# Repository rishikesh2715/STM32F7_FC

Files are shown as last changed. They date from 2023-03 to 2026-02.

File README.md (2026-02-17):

# I am going to be working on a new design of this flight controller.

- Removing AT7456E based analog OSD and CVBS routing.
- Targeting modern digital FPV systems.
- Feel free to recommend any changes you wanna see. Just open an issue.

Hoping to have the new hardware done next month if life chills out. 

# STM32F7_Based_FLight-controller
STM32F722RET6 Based Flight Controller with ICM-42688-P IMU, BMP388 Barometer, and much more!

Detailed Specification:
- MCU - STM32F722RET6
- Interial Measurement Unit (IMU) - ICM-42688-P
- Barometer - BMP388
- On-screen Display chip (OSD) - AT7456E
- SPI FLASH - W25Q256JVEIQ (256 Mbit QUAD SPI NOR FLASH)
- 9 V -- 2A Buck Converter - TPS54335ADRCR
- 5V -- 2A Buck Converter - TPS54335ADRCR
- 3.3 V -- 700 mA LDO - AZ1117-3.3

Connectors:
- 4 UARTs
- 3 SPIs
- 1 I2C

This flight controller is directly flashable and configurale via BetaFlight. Make sure to flash the FC with custom CLI file named "IRS_CLI". There is a official tutorial on youtube on how to flash a custom flight controller with a custom cli file.

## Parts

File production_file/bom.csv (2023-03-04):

Designator | Footprint | Quantity | Value | LCSC Part #
TP19 | Solderable Point | 1 | G
TP6 | Solderable Point | 1 | G
TP5 | Solderable Point | 1 | G
D3 | LED_0402_1005Metric | 1 | LED
C39 | C_0201_0603Metric | 1 | 100n
TP4 | Solderable Point | 1 | DJI_RX
TP8 | Solderable Point | 1 | G
TP12 | Solderable Point | 1 | 3.3V
TP11 | Solderable Point | 1 | 3.3V
TP10 | Solderable Point | 1 | G
C46 | C_0201_0603Metric | 1 | 100n
FB1 | R_0603_1608Metric | 1 | 120R
R14 | R_0402_1005Metric | 1 | 550R
H3 | MountingHole_2.2mm_M2_Pad_Via | 1 | MountingHole
R6 | R_0201_0603Metric | 1 | 4K7
U8 | LQFP-64_10x10mm_P0.5mm | 1 | STM32F722RET6
TP20 | Solderable Point | 1 | G
C44 | C_0402_1005Metric | 1 | 1u
TP21 | Solderable Point | 1 | G
C41 | C_0201_0603Metric | 1 | 100n
C17 | C_0805_2012Metric | 1 | 10u
R18 | R_0402_1005Metric | 1 | 10K
H4 | MountingHole_2.2mm_M2_Pad_Via | 1 | MountingHole
C38 | C_0402_1005Metric | 1 | 1u
R29 | R_0402_1005Metric | 1 | 550R
L1 | MDE0530-6R8M | 1 | 3u2, IDC 5.4A
C16 | C_0805_2012Metric | 1 | 10u
C28 | C_0603_1608Metric | 1 | 1n8
C19 | C_0805_2012Metric | 1 | 10u
H1 | MountingHole_2.2mm_M2_Pad_Via | 1 | MountingHole
C32 | C_1210_3225Metric | 1 | 47u
R27 | R_0603_1608Metric | 1 | 330R
C45 | C_0201_0603Metric | 1 | 100n
TP18 | Solderable Point | 1 | G
TP13 | Solderable Point | 1 | 5V
R16 | R_0402_1005Metric | 1 | 31K
R15 | R_0402_1005Metric | 1 | 31K
C34 | C_0402_1005Metric | 1 | 10p
D4 | LED_0402_1005Metric | 1 | LED
R11 | R_0201_0603Metric | 1 | 27R
C12 | C_0201_0603Metric | 1 | 100n
R7 | R_0201_0603Metric | 1 | 4K7
C35 | C_0402_1005Metric | 1 | 10p
TP16 | Solderable Point | 1 | 9V
C13 | C_0201_0603Metric | 1 | 100n
C42 | C_0201_0603Metric | 1 | 100n
J10 | JST_SH_SM04B-SRSS-TB_1x04-1MP_P1.00mm_Horizontal | 1 | Conn_01x04
TP2 | Solderable Point | 1 | DJI_TX
R12 | R_0201_0603Metric | 1 | 27R
J9 | Tag-Connect_TC2030-IDC-NL_2x03_P1.27mm_Vertical | 1 | TC2030-IDC-NL
TP3 | Solderable Point | 1 | GRX
C30 | C_1210_3225Metric | 1 | 47u
D5 | LED_0402_1005Metric | 1 | LED
L2 | MDE0530-6R8M | 1 | 2u7, IDC 4A
H2 | MountingHole_2.2mm_M2_Pad_Via | 1 | MountingHole
C23 | C_0402_1005Metric | 1 | 100n
TP1 | Solderable Point | 1 | GTX
C24 | C_0402_1005Metric | 1 | 100n
R13 | R_0402_1005Metric | 1 | 550R
C47 | C_0603_1608Metric | 1 | 2u2
C36 | C_0603_1608Metric | 1 | 4u7
C33 | C_1210_3225Metric | 1 | 47u
C40 | C_0201_0603Metric | 1 | 100n
U7 | TPS54335ADRCR | 1 | TPS54335ADRCR
C37 | C_0402_1005Metric | 1 | 10u
R23 | R_0402_1005Metric | 1 | 0R
Y2 | Crystal_SMD_3225-4Pin_3.2x2.5mm | 1 | 8Mhz
U6 | TPS54335ADRCR | 1 | TPS54335ADRCR
TP15 | Solderable Point | 1 | 9V
C21 | C_0402_1005Metric | 1 | 100n
C20 | C_0402_1005Metric | 1 | 100n
C26 | C_0201_0603Metric | 1 | 91p
C18 | C_0805_2012Metric | 1 | 10u
U3 | BMP388 | 1 | BMP388
J12 | JST_SH_SM06B-SRSS-TB_1x06-1MP_P1.00mm_Horizontal | 1 | Conn_01x06
C10 | C_0201_0603Metric | 1 | 10n
C22 | C_0805_2012Metric | 1 | 22u
C1 | C_0201_0603Metric | 1 | 10p
J5 | JST_SH_SM08B-SRSS-TB_1x08-1MP_P1.00mm_Horizontal | 1 | FC-ESC
C2 | C_0201_0603Metric | 1 | 10p
R20 | R_0402_1005Metric | 1 | 9K7
R1 | R_0201_0603Metric | 1 | 75R
R5 | R_0201_0603Metric | 1 | 0R
C27 | C_0603_1608Metric | 1 | 1n8
C8 | C_0201_0603Metric | 1 | 22u
J8 | JST_SH_SM06B-SRSS-TB_1x06-1MP_P1.00mm_Horizontal | 1 | Conn_01x06
Y1 | Crystal_SMD_3225-4Pin_3.2x2.5mm | 1 | 27MHz
R25 | R_0201_0603Metric | 1 | 1K
C15 | C_0805_2012Metric | 1 | 10u
Q1 | SOT-23 | 1 | DMG3415
C3 | C_0201_0603Metric | 1 | 100n
R19 | R_0402_1005Metric | 1 | 100K
U4 | SON127P600X800X80-9N | 1 | W25Q256JVEIQ
J2 | JST_SH_SM03B-SRSS-TB_1x03-1MP_P1.00mm_Horizontal | 1 | Conn_01x03
C43 | C_0402_1005Metric | 1 | 0.1u
R3 | R_0201_0603Metric | 1 | 75R
C6 | C_0201_0603Metric | 1 | 100n
R2 | R_0201_0603Metric | 1 | 10K
C5 | C_0201_0603Metric | 1 | 22u
C25 | C_0201_0603Metric | 1 | 91p
R10 | R_0201_0603Metric | 1 | 5K1
SW1 | SSSS810701 | 1 | SW_SPDT
J1 | JST_SH_SM03B-SRSS-TB_1x03-1MP_P1.00mm_Horizontal | 1 | Conn_01x03
C4 | C_0402_1005Metric | 1 | 0.1u
U5 | SOT-223-3_TabPin2 | 1 | AZ1117-ADJ
J6 | JST_SH_SM04B-SRSS-TB_1x04-1MP_P1.00mm_Horizontal | 1 | Conn_01x04
C9 | C_0201_0603Metric | 1 | 100n
J3 | JST_SH_SM03B-SRSS-TB_1x03-1MP_P1.00mm_Horizontal | 1 | Conn_01x03
R22 | R_0201_0603Metric | 1 | 19K1
D1 | D_SOD-123 | 1 | RB088LAM-40TFR
R9 | R_0201_0603Metric | 1 | 5K1
R26 | R_0402_1005Metric | 1 | 10K
C7 | C_0603_1608Metric | 1 | 2u2
R17 | R_0402_1005Metric | 1 | 10K
C29 | C_1210_3225Metric | 1 | 47u
C14 | C_0402_1005Metric | 1 | 100n
C11 | C_0201_0603Metric | 1 | 100n
R24 | R_0201_0603Metric | 1 | 10K
C31 | C_1210_3225Metric | 1 | 47u
J4 | JST_SH_SM03B-SRSS-TB_1x03-1MP_P1.00mm_Horizontal | 1 | Conn_01x03
J11 | JST_SH_SM04B-SRSS-TB_1x04-1MP_P1.00mm_Horizontal | 1 | Conn_01x04
R8 | R_0201_0603Metric | 1 | 10K
D2 | SOT-143 | 1 | PRTR5V0U2X
JP1 | SolderJumper-2_P1.3mm_Open_TrianglePad1.0x1.5mm | 1 | NRST
U2 | SOP65P637X110-28N | 1 | AT7456E
R21 | R_0201_0603Metric | 1 | 100K
J7 | JST_SH_SM06B-SRSS-TB_1x06-1MP_P1.00mm_Horizontal | 1 | DJI Air Unit
P1 | USB4110GFA | 1 | USB_C_Plug_USB2.0
R4 | R_0201_0603Metric | 1 | 0R
R28 | R_0201_0603Metric | 1 | 100K
U1 | ICP-42688-P | 1 | ICM-42688-P

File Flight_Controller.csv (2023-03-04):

Source: | C:\Users\RISHIKESH\OneDrive\Documents\Flight Controller\Flight_Controller\Flight_Controller.kicad_sch
Date: | 1/20/2023 8:09:45 PM
Tool: | Eeschema (6.0.4)
Generator: | E:\New folder (2)\Streamlabs OBS\KiCad\6.0\bin\scripting\plugins/bom_csv_grouped_by_value.py
Component Count: | 131
Individual Components:
Item | Qty | Reference(s) | Value | LibPart | Footprint | Datasheet | MANUFACTURER | MAXIMUM_PACKAGE_HEIGHT | Manufacturer | PARTREV | Package | STANDARD
 |  | C1 | 10p | Device:C_Small | Capacitor_SMD:C_0201_0603Metric | ~
 |  | C2 | 10p | Device:C_Small | Capacitor_SMD:C_0201_0603Metric | ~
 |  | C3 | 100n | Device:C_Small | Capacitor_SMD:C_0201_0603Metric | ~
 |  | C4 | 0.1u | Device:C_Small | Capacitor_SMD:C_0402_1005Metric | ~
 |  | C5 | 22u | Device:C_Small | Capacitor_SMD:C_0201_0603Metric | ~
 |  | C6 | 100n | Device:C_Small | Capacitor_SMD:C_0201_0603Metric | ~
 |  | C7 | 2u2 | Device:C_Small | Capacitor_SMD:C_0603_1608Metric | ~
 |  | C8 | 22u | Device:C_Small | Capacitor_SMD:C_0201_0603Metric | ~
 |  | C9 | 100n | Device:C_Small | Capacitor_SMD:C_0201_0603Metric | ~
 |  | C10 | 10n | Device:C_Small | Capacitor_SMD:C_0201_0603Metric | ~
 |  | C11 | 100n | Device:C_Small | Capacitor_SMD:C_0201_0603Metric | ~
 |  | C12 | 100n | Device:C_Small | Capacitor_SMD:C_0201_0603Metric | ~
 |  | C13 | 100n | Device:C_Small | Capacitor_SMD:C_0201_0603Metric | ~
 |  | C14 | 100n | Device:C_Small | Capacitor_SMD:C_0402_1005Metric | ~
 |  | C15 | 10u | Device:C_Small | Capacitor_SMD:C_0805_2012Metric | ~
 |  | C16 | 10u | Device:C_Small | Capacitor_SMD:C_0805_2012Metric | ~
 |  | C17 | 10u | Device:C_Small | Capacitor_SMD:C_0805_2012Metric | ~
 |  | C18 | 10u | Device:C_Small | Capacitor_SMD:C_0805_2012Metric | ~
 |  | C19 | 10u | Device:C_Small | Capacitor_SMD:C_0805_2012Metric | ~
 |  | C20 | 100n | Device:C_Small | Capacitor_SMD:C_0402_1005Metric | ~
 |  | C21 | 100n | Device:C_Small | Capacitor_SMD:C_0402_1005Metric | ~
 |  | C22 | 22u | Device:C_Small | Capacitor_SMD:C_0805_2012Metric | ~
 |  | C23 | 100n | Device:C_Small | Capacitor_SMD:C_0402_1005Metric | ~
 |  | C24 | 100n | Device:C_Small | Capacitor_SMD:C_0402_1005Metric | ~
 |  | C25 | 91p | Device:C_Small | Capacitor_SMD:C_0201_0603Metric | ~
 |  | C26 | 91p | Device:C_Small | Capacitor_SMD:C_0201_0603Metric | ~
 |  | C27 | 1n8 | Device:C_Small | Capacitor_SMD:C_0603_1608Metric | ~
 |  | C28 | 1n8 | Device:C_Small | Capacitor_SMD:C_0603_1608Metric | ~
 |  | C29 | 47u | Device:C_Small | Capacitor_SMD:C_1210_3225Metric | ~
 |  | C30 | 47u | Device:C_Small | Capacitor_SMD:C_1210_3225Metric | ~
 |  | C31 | 47u | Device:C_Small | Capacitor_SMD:C_1210_3225Metric | ~
 |  | C32 | 47u | Device:C_Small | Capacitor_SMD:C_1210_3225Metric | ~
 |  | C33 | 47u | Device:C_Small | Capacitor_SMD:C_1210_3225Metric | ~
 |  | C34 | 10p | Device:C_Small | Capacitor_SMD:C_0402_1005Metric | ~
 |  | C35 | 10p | Device:C_Small | Capacitor_SMD:C_0402_1005Metric | ~
 |  | C36 | 4u7 | Device:C_Small | Capacitor_SMD:C_0603_1608Metric | ~
 |  | C37 | 10u | Device:C | Capacitor_SMD:C_0402_1005Metric | ~
 |  | C38 | 1u | Device:C | Capacitor_SMD:C_0402_1005Metric | ~
 |  | C39 | 100n | Device:C | Capacitor_SMD:C_0201_0603Metric | ~
 |  | C40 | 100n | Device:C | Capacitor_SMD:C_0201_0603Metric | ~
 |  | C41 | 100n | Device:C | Capacitor_SMD:C_0201_0603Metric | ~
 |  | C42 | 100n | Device:C | Capacitor_SMD:C_0201_0603Metric | ~
 |  | C43 | 0.1u | Device:C_Small | Capacitor_SMD:C_0402_1005Metric | ~
 |  | C44 | 1u | Device:C | Capacitor_SMD:C_0402_1005Metric | ~
 |  | C45 | 100n | Device:C | Capacitor_SMD:C_0201_0603Metric | ~
 |  | C46 | 100n | Device:C | Capacitor_SMD:C_0201_0603Metric | ~
 |  | C47 | 2u2 | Device:C_Small | Capacitor_SMD:C_0603_1608Metric | ~
 |  | D1 | RB088LAM-40TFR | Device:D_Schottky | Diode_SMD:D_SOD-123 | ~
 |  | D2 | PRTR5V0U2X | Power_Protection:PRTR5V0U2X | Package_TO_SOT_SMD:SOT-143 | https://assets.nexperia.com/documents/data-sheet/PRTR5V0U2X.pdf
 |  | D3 | LED | Device:LED | LED_SMD:LED_0402_1005Metric | ~
 |  | D4 | LED | Device:LED | LED_SMD:LED_0402_1005Metric | ~
 |  | D5 | LED | Device:LED | LED_SMD:LED_0402_1005Metric | ~
 |  | FB1 | 120R | Device:FerriteBead | Resistor_SMD:R_0603_1608Metric | ~
 |  | H1 | MountingHole | Mechanical:MountingHole | MountingHole:MountingHole_2.2mm_M2_Pad_Via | ~
 |  | H2 | MountingHole | Mechanical:MountingHole | MountingHole:MountingHole_2.2mm_M2_Pad_Via | ~
 |  | H3 | MountingHole | Mechanical:MountingHole | MountingHole:MountingHole_2.2mm_M2_Pad_Via | ~
 |  | H4 | MountingHole | Mechanical:MountingHole | MountingHole:MountingHole_2.2mm_M2_Pad_Via | ~
 |  | J1 | Conn_01x03 | Connector_Generic:Conn_01x03 | Connector_JST:JST_SH_SM03B-SRSS-TB_1x03-1MP_P1.00mm_Horizontal | ~
 |  | J2 | Conn_01x03 | Connector_Generic:Conn_01x03 | Connector_JST:JST_SH_SM03B-SRSS-TB_1x03-1MP_P1.00mm_Horizontal | ~
 |  | J3 | Conn_01x03 | Connector_Generic:Conn_01x03 | Connector_JST:JST_SH_SM03B-SRSS-TB_1x03-1MP_P1.00mm_Horizontal | ~
 |  | J4 | Conn_01x03 | Connector_Generic:Conn_01x03 | Connector_JST:JST_SH_SM03B-SRSS-TB_1x03-1MP_P1.00mm_Horizontal | ~
 |  | J5 | FC-ESC | SM08B-SRSS-TB_LF__SN_:SM08B-SRSS-TB(LF)(SN) | Connector_JST:JST_SH_SM08B-SRSS-TB_1x08-1MP_P1.00mm_Horizontal |  | JST
 |  | J6 | Conn_01x04 | Connector_Generic:Conn_01x04 | Connector_JST:JST_SH_SM04B-SRSS-TB_1x04-1MP_P1.00mm_Horizontal | ~
 |  | J7 | DJI Air Unit | Connector_Generic:Conn_01x06 | Connector_JST:JST_SH_SM06B-SRSS-TB_1x06-1MP_P1.00mm_Horizontal | ~
 |  | J8 | Conn_01x06 | Connector_Generic:Conn_01x06 | Connector_JST:JST_SH_SM06B-SRSS-TB_1x06-1MP_P1.00mm_Horizontal | ~
 |  | J9 | TC2030-IDC-NL | Connector:TC2030-IDC-NL | Connector:Tag-Connect_TC2030-IDC-NL_2x03_P1.27mm_Vertical
 |  | J10 | Conn_01x04 | Connector_Generic:Conn_01x04 | Connector_JST:JST_SH_SM04B-SRSS-TB_1x04-1MP_P1.00mm_Horizontal | ~
 |  | J11 | Conn_01x04 | Connector_Generic:Conn_01x04 | Connector_JST:JST_SH_SM04B-SRSS-TB_1x04-1MP_P1.00mm_Horizontal | ~
 |  | J12 | Conn_01x06 | Connector_Generic:Conn_01x06 | Connector_JST:JST_SH_SM06B-SRSS-TB_1x06-1MP_P1.00mm_Horizontal | ~
 |  | JP1 | NRST | Jumper:SolderJumper_2_Open | Jumper:SolderJumper-2_P1.3mm_Open_TrianglePad1.0x1.5mm | ~
 |  | L1 | 3u2, IDC 5.4A | Device:L_Small | Inductor_SMD:MDE0530-6R8M | ~
 |  | L2 | 2u7, IDC 4A | Device:L_Small | Inductor_SMD:MDE0530-6R8M | ~
 |  | P1 | USB_C_Plug_USB2.0 | Connector:USB_C_Plug_USB2.0 | USB4110-GF-A:USB4110GFA | https://www.usb.org/sites/default/files/documents/usb_type-c.zip
 |  | Q1 | DMG3415 | Transistor_FET:DMG2301L | Package_TO_SOT_SMD:SOT-23 | https://www.diodes.com/assets/Datasheets/DMG2301L.pdf
 |  | R1 | 75R | Device:R_Small_US | Resistor_SMD:R_0201_0603Metric | ~
 |  | R2 | 10K | Device:R_Small_US | Resistor_SMD:R_0201_0603Metric | ~
 |  | R3 | 75R | Device:R_Small_US | Resistor_SMD:R_0201_0603Metric | ~
 |  | R4 | 0R | Device:R_Small_US | Resistor_SMD:R_0201_0603Metric | ~
 |  | R5 | 0R | Device:R_Small_US | Resistor_SMD:R_0201_0603Metric | ~
 |  | R6 | 4K7 | Device:R_Small_US | Resistor_SMD:R_0201_0603Metric | ~
 |  | R7 | 4K7 | Device:R_Small_US | Resistor_SMD:R_0201_0603Metric | ~
 |  | R8 | 10K | Device:R_Small_US | Resistor_SMD:R_0201_0603Metric | ~
 |  | R9 | 5K1 | Device:R_Small_US | Resistor_SMD:R_0201_0603Metric | ~
 |  | R10 | 5K1 | Device:R_Small_US | Resistor_SMD:R_0201_0603Metric | ~
 |  | R11 | 27R | Device:R_Small_US | Resistor_SMD:R_0201_0603Metric | ~
 |  | R12 | 27R | Device:R_Small_US | Resistor_SMD:R_0201_0603Metric | ~
 |  | R13 | 550R | Device:R_Small_US | Resistor_SMD:R_0402_1005Metric | ~
 |  | R14 | 550R | Device:R_Small_US | Resistor_SMD:R_0402_1005Metric | ~
 |  | R15 | 31K | Device:R_Small_US | Resistor_SMD:R_0402_1005Metric | ~
 |  | R16 | 31K | Device:R_Small_US | Resistor_SMD:R_0402_1005Metric | ~
 |  | R17 | 10K | Device:R_Small_US | Resistor_SMD:R_0402_1005Metric | ~
 |  | R18 | 10K | Device:R_Small_US | Resistor_SMD:R_0402_1005Metric | ~
 |  | R19 | 100K | Device:R_Small_US | Resistor_SMD:R_0402_1005Metric | ~
 |  | R20 | 9K7 | Device:R_Small_US | Resistor_SMD:R_0402_1005Metric | ~
 |  | R21 | 100K | Device:R_Small_US | Resistor_SMD:R_0201_0603Metric | ~
 |  | R22 | 19K1 | Device:R_Small_US | Resistor_SMD:R_0201_0603Metric | ~
 |  | R23 | 0R | Device:R_Small_US | Resistor_SMD:R_0402_1005Metric | ~
 |  | R24 | 10K | Device:R_Small_US | Resistor_SMD:R_0201_0603Metric | ~
 |  | R25 | 1K | Device:R_Small_US | Resistor_SMD:R_0201_0603Metric | ~
 |  | R26 | 10K | Device:R_Small_US | Resistor_SMD:R_0402_1005Metric | ~
 |  | R27 | 330R | Device:R_Small_US | Resistor_SMD:R_0603_1608Metric | ~
 |  | R28 | 100K | Device:R_Small_US | Resistor_SMD:R_0201_0603Metric | ~
 |  | R29 | 550R | Device:R_Small_US | Resistor_SMD:R_0402_1005Metric | ~
 |  | SW1 | SW_SPDT | Switch:SW_SPDT | SamacSys_Parts:SSSS810701 | ~
 |  | TP1 | GTX | Connector:TestPoint | TestPoint:Solderable Point | ~
 |  | TP2 | DJI_TX | Connector:TestPoint | TestPoint:Solderable Point | ~
 |  | TP3 | GRX | Connector:TestPoint | TestPoint:Solderable Point | ~
 |  | TP4 | DJI_RX | Connector:TestPoint | TestPoint:Solderable Point | ~
 |  | TP5 | G | Connector:TestPoint | TestPoint:Solderable Point | ~
 |  | TP6 | G | Connector:TestPoint | TestPoint:Solderable Point | ~
 |  | TP8 | G | Connector:TestPoint | TestPoint:Solderable Point | ~
 |  | TP10 | G | Connector:TestPoint | TestPoint:Solderable Point | ~
 |  | TP11 | 3.3V | Connector:TestPoint | TestPoint:Solderable Point | ~
 |  | TP12 | 3.3V | Connector:TestPoint | TestPoint:Solderable Point | ~
 |  | TP13 | 5V | Connector:TestPoint | TestPoint:Solderable Point | ~
 |  | TP15 | 9V | Connector:TestPoint | TestPoint:Solderable Point | ~
 |  | TP16 | 9V | Connector:TestPoint | TestPoint:Solderable Point | ~
 |  | TP18 | G | Connector:TestPoint | TestPoint:Solderable Point | ~
 |  | TP19 | G | Connector:TestPoint | TestPoint:Solderable Point | ~
 |  | TP20 | G | Connector:TestPoint | TestPoint:Solderable Point | ~
 |  | TP21 | G | Connector:TestPoint | TestPoint:Solderable Point | ~
 |  | U1 | ICM-42688-P | ICM-42688-P:ICM-42688-P | ICM-42688-P:ICP-42688-P |  | TDK InvenSense | 0.97mm |  | 1.2 |  | IPC-7351B
 |  | U2 | AT7456E | MAX7456EUI_:MAX7456EUI+ | MAX7456EUI_:SOP65P637X110-28N
 |  | U3 | BMP388 | BMP388:BMP388 | BMP388:BMP388 |  | BOSCH |  |  | 1.1 |  | IPC 7351B
 |  | U4 | W25Q256JVEIQ | W25Q256JVEIQ:W25Q256JVEIQ | W25Q256JVEIQ:SON127P600X800X80-9N |  |  |  | Winbond Electronics |  | SON127P600X800X80-9N
 |  | U5 | AZ1117-ADJ | Regulator_Linear:AZ1117-ADJ | Package_TO_SOT_SMD:SOT-223-3_TabPin2 | https://www.diodes.com/assets/Datasheets/AZ1117.pdf
 |  | U6 | TPS54335ADRCR | TPS54335ADRCR:TPS54335ADRCR | TPS54335ADRC:TPS54335ADRCR
 |  | U7 | TPS54335ADRCR | TPS54335ADRCR:TPS54335ADRCR | TPS54335ADRC:TPS54335ADRCR
 |  | U8 | STM32F722RET6 | MCU_ST_STM32F7:STM32F722RETx | Package_QFP:LQFP-64_10x10mm_P0.5mm | http://www.st.com/st-web-ui/static/active/en/resource/technical/document/datasheet/DM00330506.pdf
 |  | Y1 | 27MHz | Device:Crystal_GND24 | Crystal:Crystal_SMD_3225-4Pin_3.2x2.5mm | ~
 |  | Y2 | 8Mhz | Device:Crystal_GND24 | Crystal:Crystal_SMD_3225-4Pin_3.2x2.5mm | ~
Collated Components:
Item | Qty | Reference(s) | Value | LibPart | Footprint | Datasheet | MANUFACTURER | MAXIMUM_PACKAGE_HEIGHT | Manufacturer | PARTREV | Package | STANDARD
1 | 2 | C1, C2 | 10p | Device:C_Small | Capacitor_SMD:C_0201_0603Metric | ~
2 | 6 | C3, C6, C9, C11, C12, C13 | 100n | Device:C_Small | Capacitor_SMD:C_0201_0603Metric | ~
3 | 2 | C4, C43 | 0.1u | Device:C_Small | Capacitor_SMD:C_0402_1005Metric | ~
4 | 2 | C5, C8 | 22u | Device:C_Small | Capacitor_SMD:C_0201_0603Metric | ~
5 | 2 | C7, C47 | 2u2 | Device:C_Small | Capacitor_SMD:C_0603_1608Metric | ~
6 | 1 | C10 | 10n | Device:C_Small | Capacitor_SMD:C_0201_0603Metric | ~
7 | 5 | C14, C20, C21, C23, C24 | 100n | Device:C_Small | Capacitor_SMD:C_0402_1005Metric | ~
8 | 5 | C15, C16, C17, C18, C19 | 10u | Device:C_Small | Capacitor_SMD:C_0805_2012Metric | ~
9 | 1 | C22 | 22u | Device:C_Small | Capacitor_SMD:C_0805_2012Metric | ~
10 | 2 | C25, C26 | 91p | Device:C_Small | Capacitor_SMD:C_0201_0603Metric | ~
11 | 2 | C27, C28 | 1n8 | Device:C_Small | Capacitor_SMD:C_0603_1608Metric | ~
12 | 5 | C29, C30, C31, C32, C33 | 47u | Device:C_Small | Capacitor_SMD:C_1210_3225Metric | ~
13 | 2 | C34, C35 | 10p | Device:C_Small | Capacitor_SMD:C_0402_1005Metric | ~
14 | 1 | C36 | 4u7 | Device:C_Small | Capacitor_SMD:C_0603_1608Metric | ~
15 | 1 | C37 | 10u | Device:C | Capacitor_SMD:C_0402_1005Metric | ~
16 | 2 | C38, C44 | 1u | Device:C | Capacitor_SMD:C_0402_1005Metric | ~
17 | 6 | C39, C40, C41, C42, C45, C46 | 100n | Device:C | Capacitor_SMD:C_0201_0603Metric | ~
18 | 1 | D1 | RB088LAM-40TFR | Device:D_Schottky | Diode_SMD:D_SOD-123 | ~
19 | 1 | D2 | PRTR5V0U2X | Power_Protection:PRTR5V0U2X | Package_TO_SOT_SMD:SOT-143 | https://assets.nexperia.com/documents/data-sheet/PRTR5V0U2X.pdf
20 | 3 | D3, D4, D5 | LED | Device:LED | LED_SMD:LED_0402_1005Metric | ~
21 | 1 | FB1 | 120R | Device:FerriteBead | Resistor_SMD:R_0603_1608Metric | ~
22 | 4 | H1, H2, H3, H4 | MountingHole | Mechanical:MountingHole | MountingHole:MountingHole_2.2mm_M2_Pad_Via | ~
23 | 4 | J1, J2, J3, J4 | Conn_01x03 | Connector_Generic:Conn_01x03 | Connector_JST:JST_SH_SM03B-SRSS-TB_1x03-1MP_P1.00mm_Horizontal | ~
24 | 1 | J5 | FC-ESC | SM08B-SRSS-TB_LF__SN_:SM08B-SRSS-TB(LF)(SN) | Connector_JST:JST_SH_SM08B-SRSS-TB_1x08-1MP_P1.00mm_Horizontal |  | JST
25 | 3 | J6, J10, J11 | Conn_01x04 | Connector_Generic:Conn_01x04 | Connector_JST:JST_SH_SM04B-SRSS-TB_1x04-1MP_P1.00mm_Horizontal | ~
26 | 1 | J7 | DJI Air Unit | Connector_Generic:Conn_01x06 | Connector_JST:JST_SH_SM06B-SRSS-TB_1x06-1MP_P1.00mm_Horizontal | ~
27 | 2 | J8, J12 | Conn_01x06 | Connector_Generic:Conn_01x06 | Connector_JST:JST_SH_SM06B-SRSS-TB_1x06-1MP_P1.00mm_Horizontal | ~
28 | 1 | J9 | TC2030-IDC-NL | Connector:TC2030-IDC-NL | Connector:Tag-Connect_TC2030-IDC-NL_2x03_P1.27mm_Vertical
29 | 1 | JP1 | NRST | Jumper:SolderJumper_2_Open | Jumper:SolderJumper-2_P1.3mm_Open_TrianglePad1.0x1.5mm | ~
30 | 1 | L1 | 3u2, IDC 5.4A | Device:L_Small | Inductor_SMD:MDE0530-6R8M | ~
31 | 1 | L2 | 2u7, IDC 4A | Device:L_Small | Inductor_SMD:MDE0530-6R8M | ~
32 | 1 | P1 | USB_C_Plug_USB2.0 | Connector:USB_C_Plug_USB2.0 | USB4110-GF-A:USB4110GFA | https://www.usb.org/sites/default/files/documents/usb_type-c.zip
33 | 1 | Q1 | DMG3415 | Transistor_FET:DMG2301L | Package_TO_SOT_SMD:SOT-23 | https://www.diodes.com/assets/Datasheets/DMG2301L.pdf
34 | 2 | R1, R3 | 75R | Device:R_Small_US | Resistor_SMD:R_0201_0603Metric | ~
35 | 3 | R2, R8, R24 | 10K | Device:R_Small_US | Resistor_SMD:R_0201_0603Metric | ~
36 | 2 | R4, R5 | 0R | Device:R_Small_US | Resistor_SMD:R_0201_0603Metric | ~
37 | 2 | R6, R7 | 4K7 | Device:R_Small_US | Resistor_SMD:R_0201_0603Metric | ~
38 | 2 | R9, R10 | 5K1 | Device:R_Small_US | Resistor_SMD:R_0201_0603Metric | ~
39 | 2 | R11, R12 | 27R | Device:R_Small_US | Resistor_SMD:R_0201_0603Metric | ~
40 | 3 | R13, R14, R29 | 550R | Device:R_Small_US | Resistor_SMD:R_0402_1005Metric | ~
41 | 2 | R15, R16 | 31K | Device:R_Small_US | Resistor_SMD:R_0402_1005Metric | ~
42 | 3 | R17, R18, R26 | 10K | Device:R_Small_US | Resistor_SMD:R_0402_1005Metric | ~
43 | 1 | R19 | 100K | Device:R_Small_US | Resistor_SMD:R_0402_1005Metric | ~
44 | 1 | R20 | 9K7 | Device:R_Small_US | Resistor_SMD:R_0402_1005Metric | ~
45 | 2 | R21, R28 | 100K | Device:R_Small_US | Resistor_SMD:R_0201_0603Metric | ~
46 | 1 | R22 | 19K1 | Device:R_Small_US | Resistor_SMD:R_0201_0603Metric | ~
47 | 1 | R23 | 0R | Device:R_Small_US | Resistor_SMD:R_0402_1005Metric | ~
48 | 1 | R25 | 1K | Device:R_Small_US | Resistor_SMD:R_0201_0603Metric | ~
49 | 1 | R27 | 330R | Device:R_Small_US | Resistor_SMD:R_0603_1608Metric | ~
50 | 1 | SW1 | SW_SPDT | Switch:SW_SPDT | SamacSys_Parts:SSSS810701 | ~
51 | 1 | TP1 | GTX | Connector:TestPoint | TestPoint:Solderable Point | ~
52 | 1 | TP2 | DJI_TX | Connector:TestPoint | TestPoint:Solderable Point | ~
53 | 1 | TP3 | GRX | Connector:TestPoint | TestPoint:Solderable Point | ~
54 | 1 | TP4 | DJI_RX | Connector:TestPoint | TestPoint:Solderable Point | ~
55 | 8 | TP5, TP6, TP8, TP10, TP18, TP19, TP20, TP21 | G | Connector:TestPoint | TestPoint:Solderable Point | ~
56 | 2 | TP11, TP12 | 3.3V | Connector:TestPoint | TestPoint:Solderable Point | ~
57 | 1 | TP13 | 5V | Connector:TestPoint | TestPoint:Solderable Point | ~
58 | 2 | TP15, TP16 | 9V | Connector:TestPoint | TestPoint:Solderable Point | ~
59 | 1 | U1 | ICM-42688-P | ICM-42688-P:ICM-42688-P | ICM-42688-P:ICP-42688-P |  | TDK InvenSense | 0.97mm |  | 1.2 |  | IPC-7351B
60 | 1 | U2 | AT7456E | MAX7456EUI_:MAX7456EUI+ | MAX7456EUI_:SOP65P637X110-28N
61 | 1 | U3 | BMP388 | BMP388:BMP388 | BMP388:BMP388 |  | BOSCH |  |  | 1.1 |  | IPC 7351B
62 | 1 | U4 | W25Q256JVEIQ | W25Q256JVEIQ:W25Q256JVEIQ | W25Q256JVEIQ:SON127P600X800X80-9N |  |  |  | Winbond Electronics |  | SON127P600X800X80-9N
63 | 1 | U5 | AZ1117-ADJ | Regulator_Linear:AZ1117-ADJ | Package_TO_SOT_SMD:SOT-223-3_TabPin2 | https://www.diodes.com/assets/Datasheets/AZ1117.pdf
64 | 2 | U6, U7 | TPS54335ADRCR | TPS54335ADRCR:TPS54335ADRCR | TPS54335ADRC:TPS54335ADRCR
65 | 1 | U8 | STM32F722RET6 | MCU_ST_STM32F7:STM32F722RETx | Package_QFP:LQFP-64_10x10mm_P0.5mm | http://www.st.com/st-web-ui/static/active/en/resource/technical/document/datasheet/DM00330506.pdf
66 | 1 | Y1 | 27MHz | Device:Crystal_GND24 | Crystal:Crystal_SMD_3225-4Pin_3.2x2.5mm | ~
67 | 1 | Y2 | 8Mhz | Device:Crystal_GND24 | Crystal:Crystal_SMD_3225-4Pin_3.2x2.5mm | ~

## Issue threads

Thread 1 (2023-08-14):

firmware

JackSnowK, 2023-08-14:
which firmware can match this board which you designed in betaflight?

rishikesh2715, 2023-08-15:
Speedybee F7 V3 cli (config) file matches this FC board.
[cli betaflight.txt](https://github.com/rishikesh2715/STM32F7_FC/files/12342310/cli.betaflight.txt)

rishikesh2715, 2024-07-24:
closed

Closed 2024-07-24.

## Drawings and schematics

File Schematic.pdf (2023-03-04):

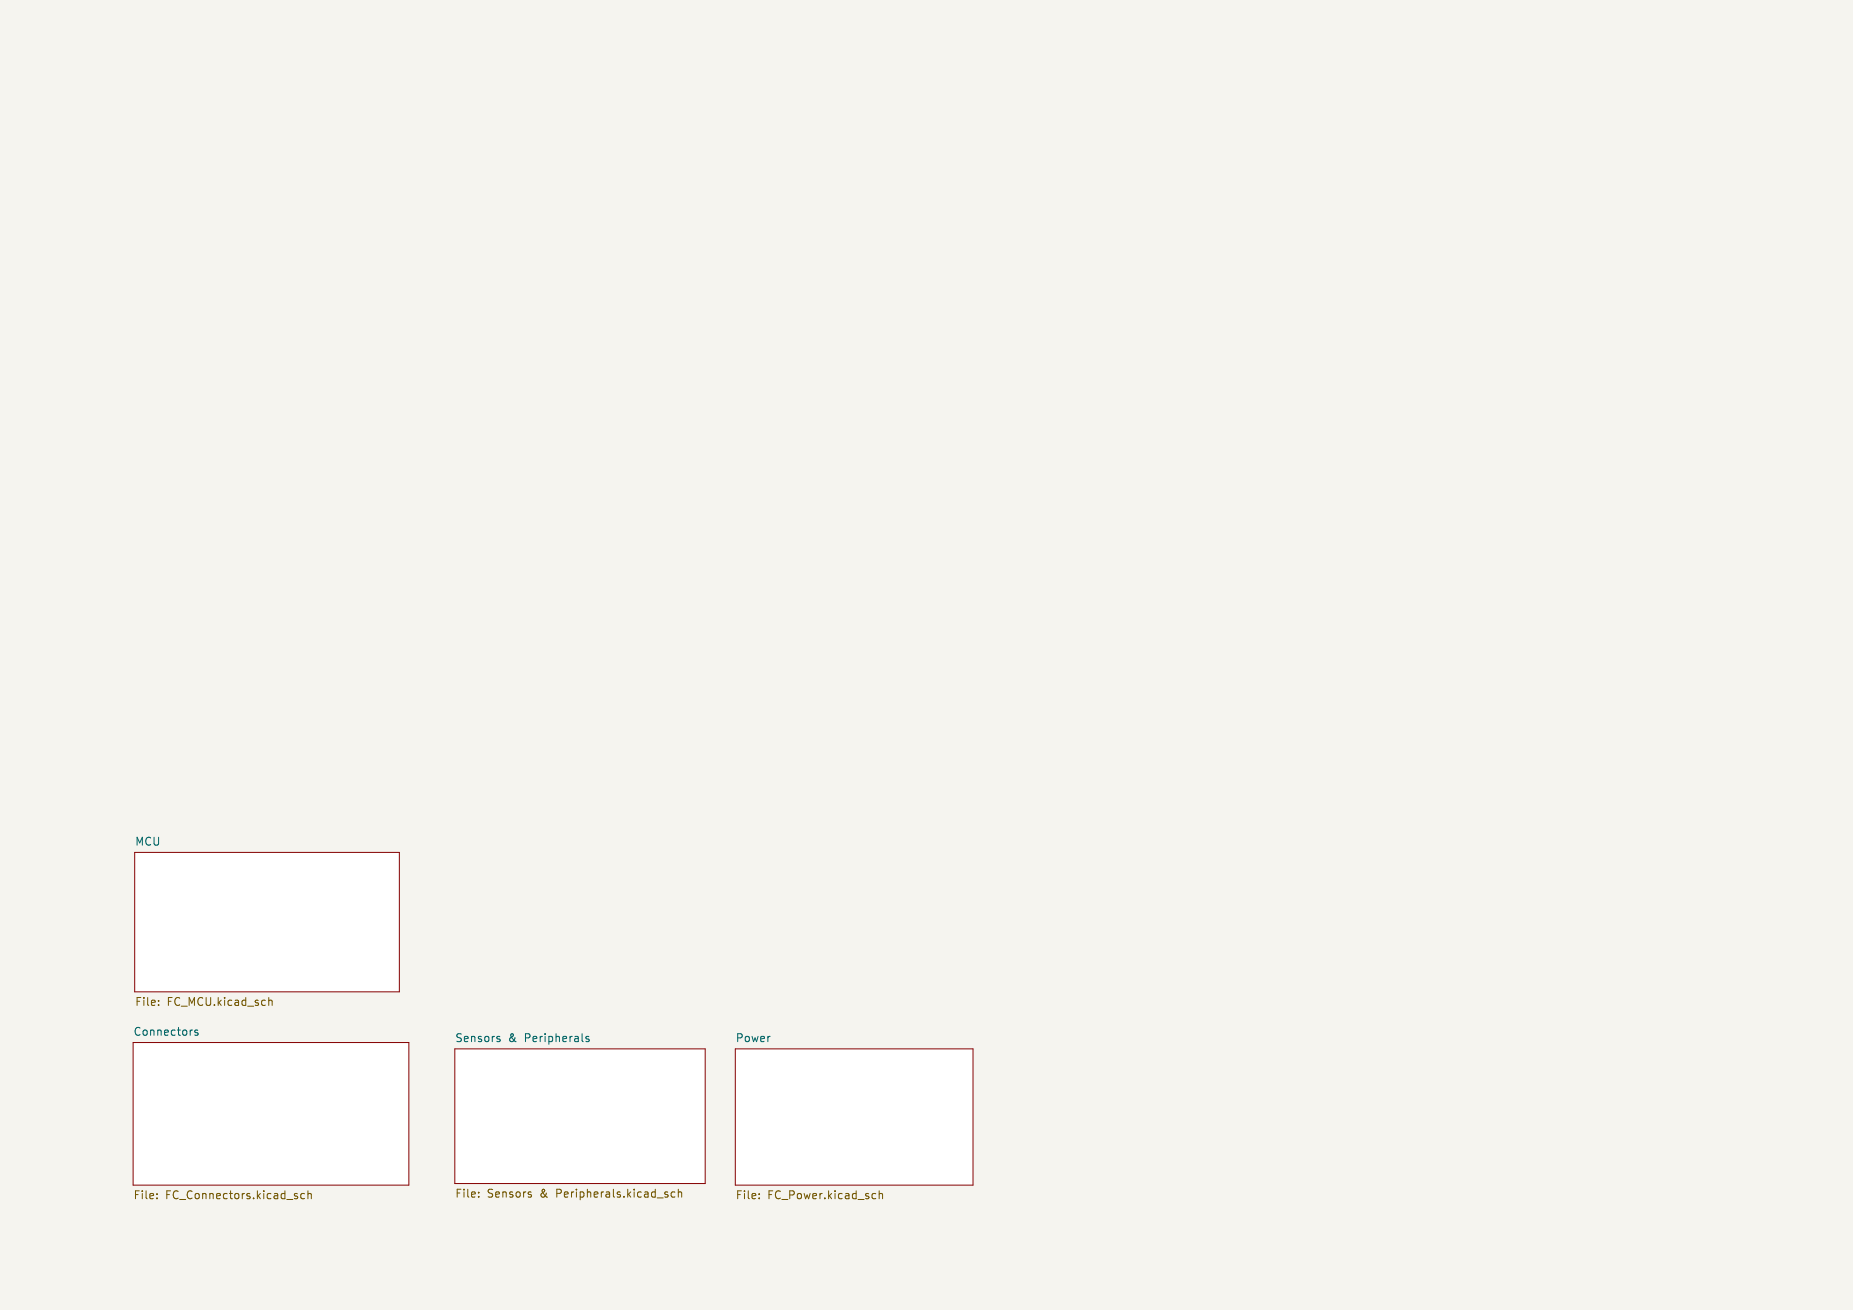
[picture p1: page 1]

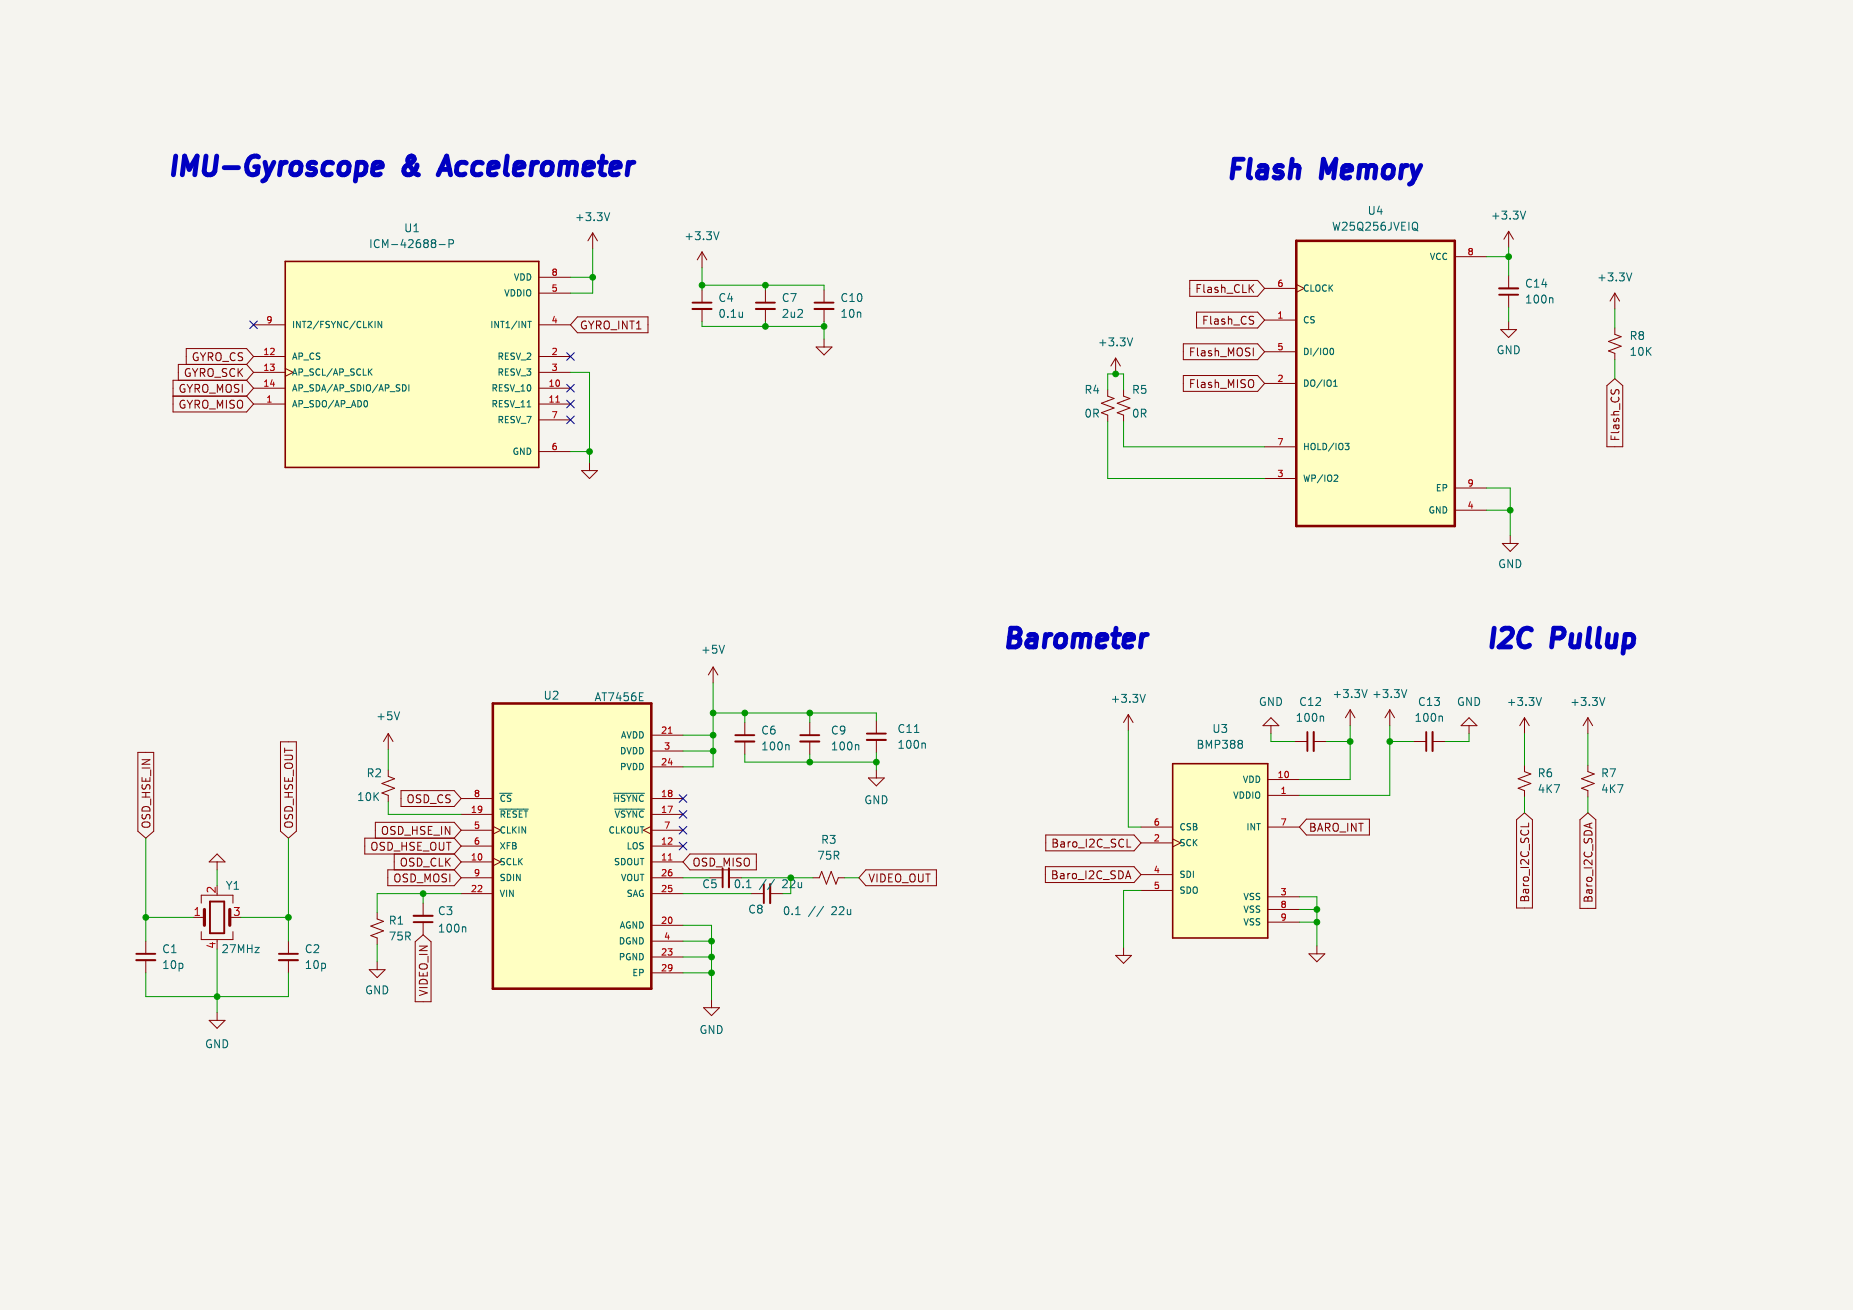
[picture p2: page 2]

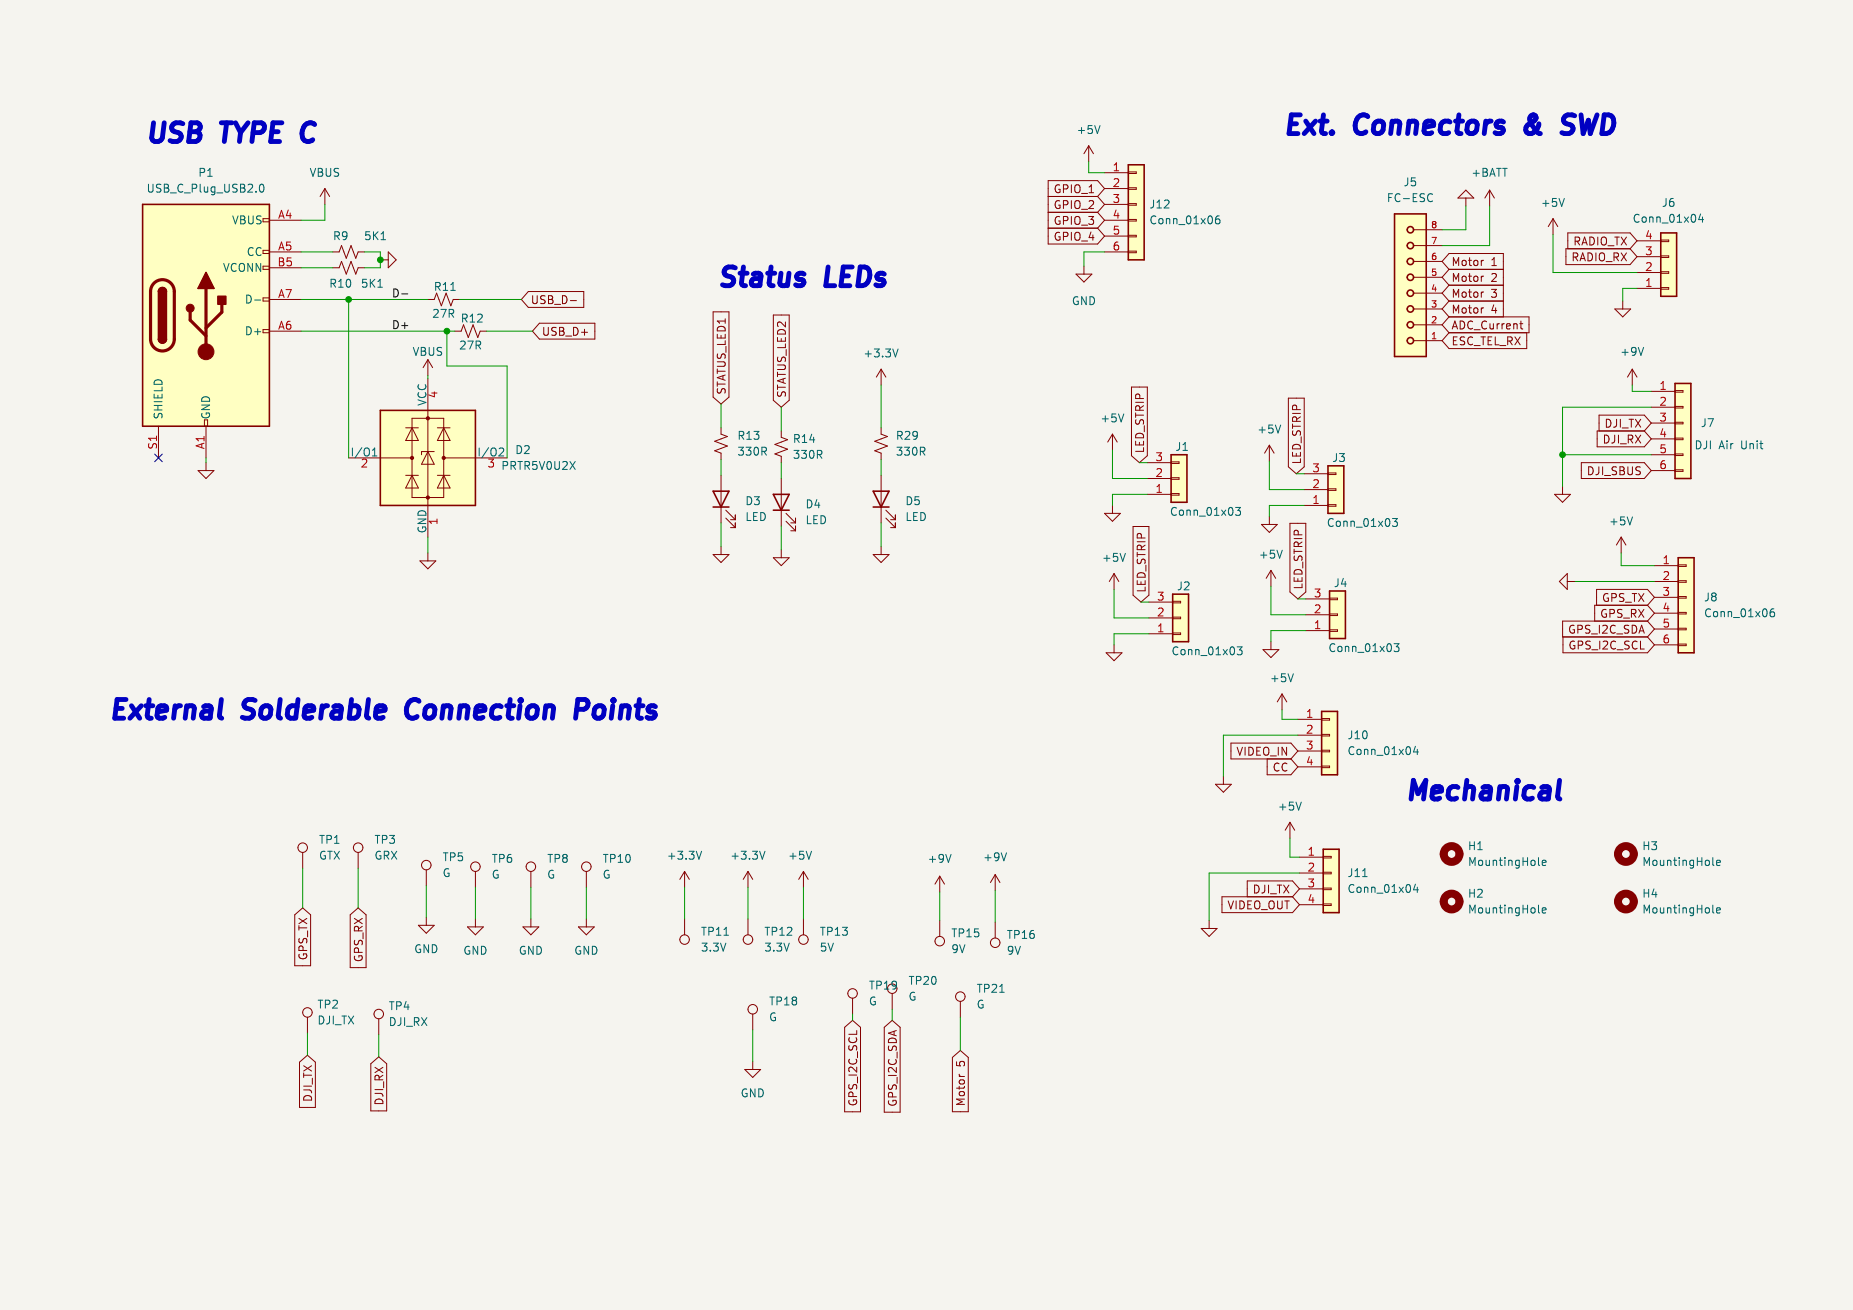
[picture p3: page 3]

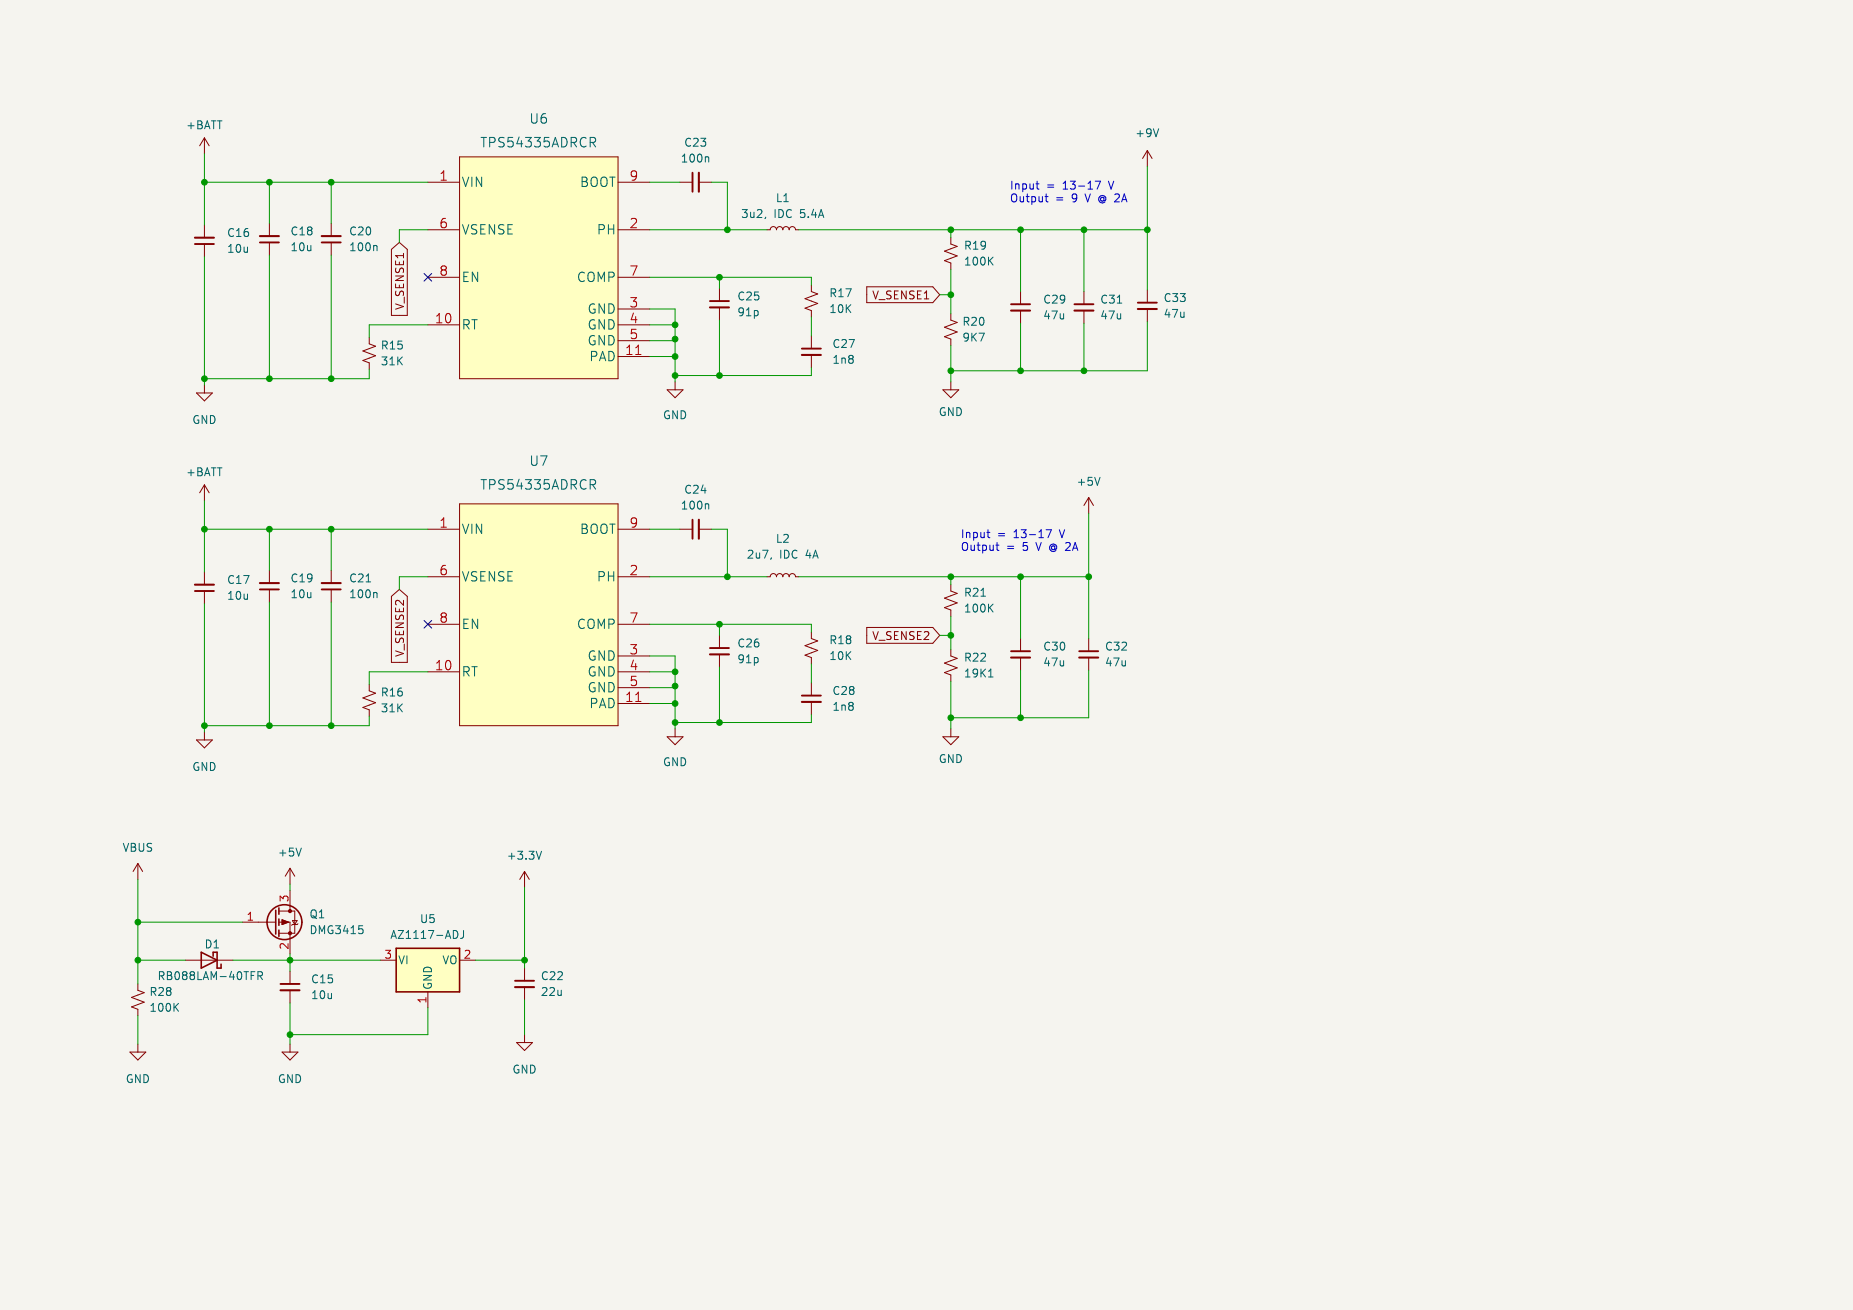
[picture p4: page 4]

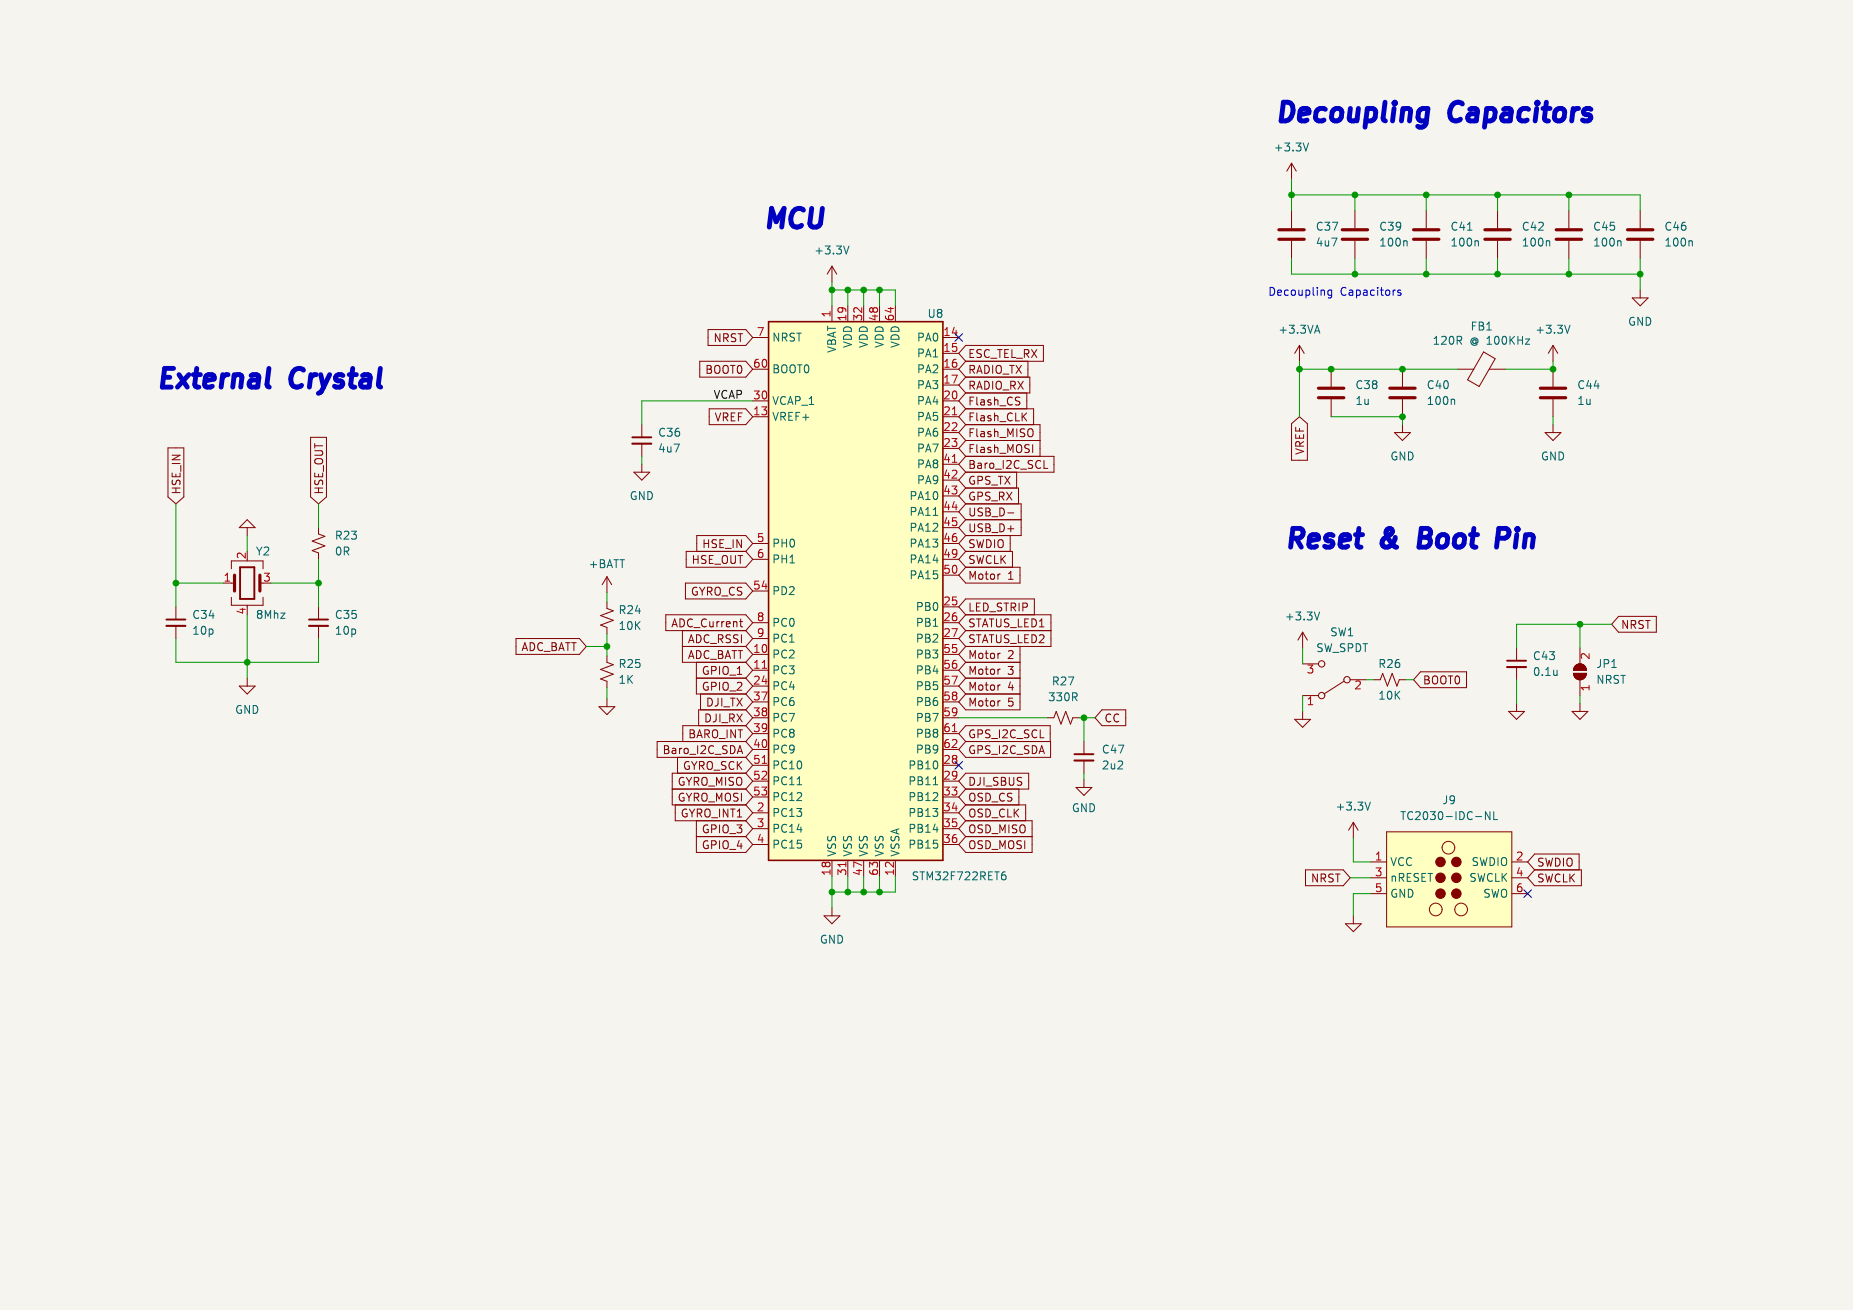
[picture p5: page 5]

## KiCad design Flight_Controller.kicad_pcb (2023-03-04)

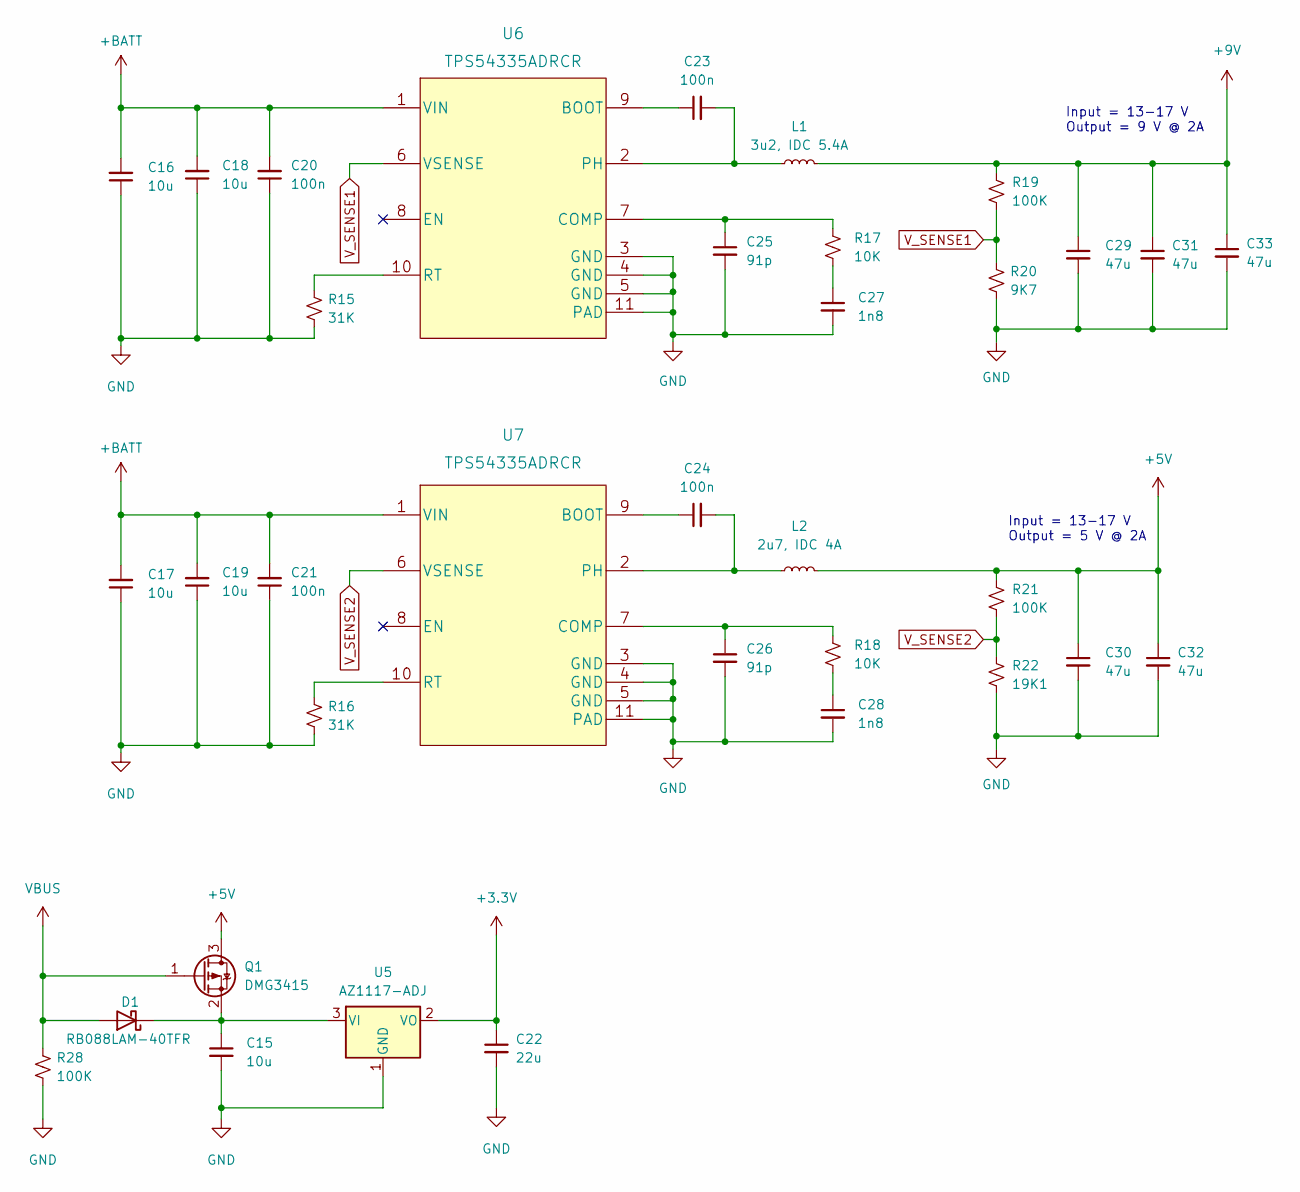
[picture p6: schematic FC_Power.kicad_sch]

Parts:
C15, C16, C17, C18, C19: 10u; C_0805_2012Metric
C20, C21, C23, C24: 100n; C_0402_1005Metric
C22: 22u; C_0805_2012Metric
C25, C26: 91p; C_0201_0603Metric
C27, C28: 1n8; C_0603_1608Metric
C29, C30, C31, C32, C33: 47u; C_1210_3225Metric
D1: RB088LAM-40TFR; D_SOD-123
L1: 3u2, IDC 5.4A; MDE0530-6R8M
L2: 2u7, IDC 4A; MDE0530-6R8M
Q1: DMG3415; SOT-23
R15, R16: 31K; R_0402_1005Metric
R17, R18: 10K; R_0402_1005Metric
R19: 100K; R_0402_1005Metric
R20: 9K7; R_0402_1005Metric
R21, R28: 100K; R_0201_0603Metric
R22: 19K1; R_0201_0603Metric
U5: AZ1117-ADJ; SOT-223-3_TabPin2
U6, U7: TPS54335ADRCR

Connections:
+3V3: C22.1, U5.2 (VO); also elsewhere on the board
+5V: C30.1, C32.1, L2.2, Q1.3 (D), R21.1; also elsewhere on the board
+9V: C29.1, C31.1, C33.1, L1.2, R19.1; also elsewhere on the board
+BATT: C16.2, C17.2, C18.2, C19.2, C20.2, C21.2, U6.1 (VIN), U7.1 (VIN); also elsewhere on the board
GND: C15.2, C16.1, C17.1, C18.1, C19.1, C20.1, C21.1, C22.2, C25.2, C26.2, C27.2, C28.2, C29.2, C30.2, C31.2, C32.2, C33.2, R15.2, R16.2, R20.2, R22.2, R28.2, U5.1 (GND), U6.3 (GND), U6.4 (GND), U6.5 (GND), U6.11 (PAD), U7.3 (GND), U7.4 (GND), U7.5 (GND), U7.11 (PAD); also elsewhere on the board
unnamed: C15.1, D1.1 (K), Q1.2 (S), U5.3 (VI)
unnamed: C23.1, U6.9 (BOOT)
unnamed: C23.2, L1.1, U6.2 (PH)
unnamed: C24.1, U7.9 (BOOT)
unnamed: C24.2, L2.1, U7.2 (PH)
unnamed: C25.1, R17.1, U6.7 (COMP)
unnamed: C26.1, R18.1, U7.7 (COMP)
unnamed: C27.1, R17.2
unnamed: C28.1, R18.2
unnamed: R15.1, U6.10 (RT)
unnamed: R16.1, U7.10 (RT)
VBUS: D1.2 (A), Q1.1 (G), R28.1; also elsewhere on the board
V_SENSE1: R19.2, R20.1, U6.6 (VSENSE)
V_SENSE2: R21.2, R22.1, U7.6 (VSENSE)

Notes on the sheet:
Input = 13-17 V Output = 9 V @ 2A
Input = 13-17 V Output = 5 V @ 2A

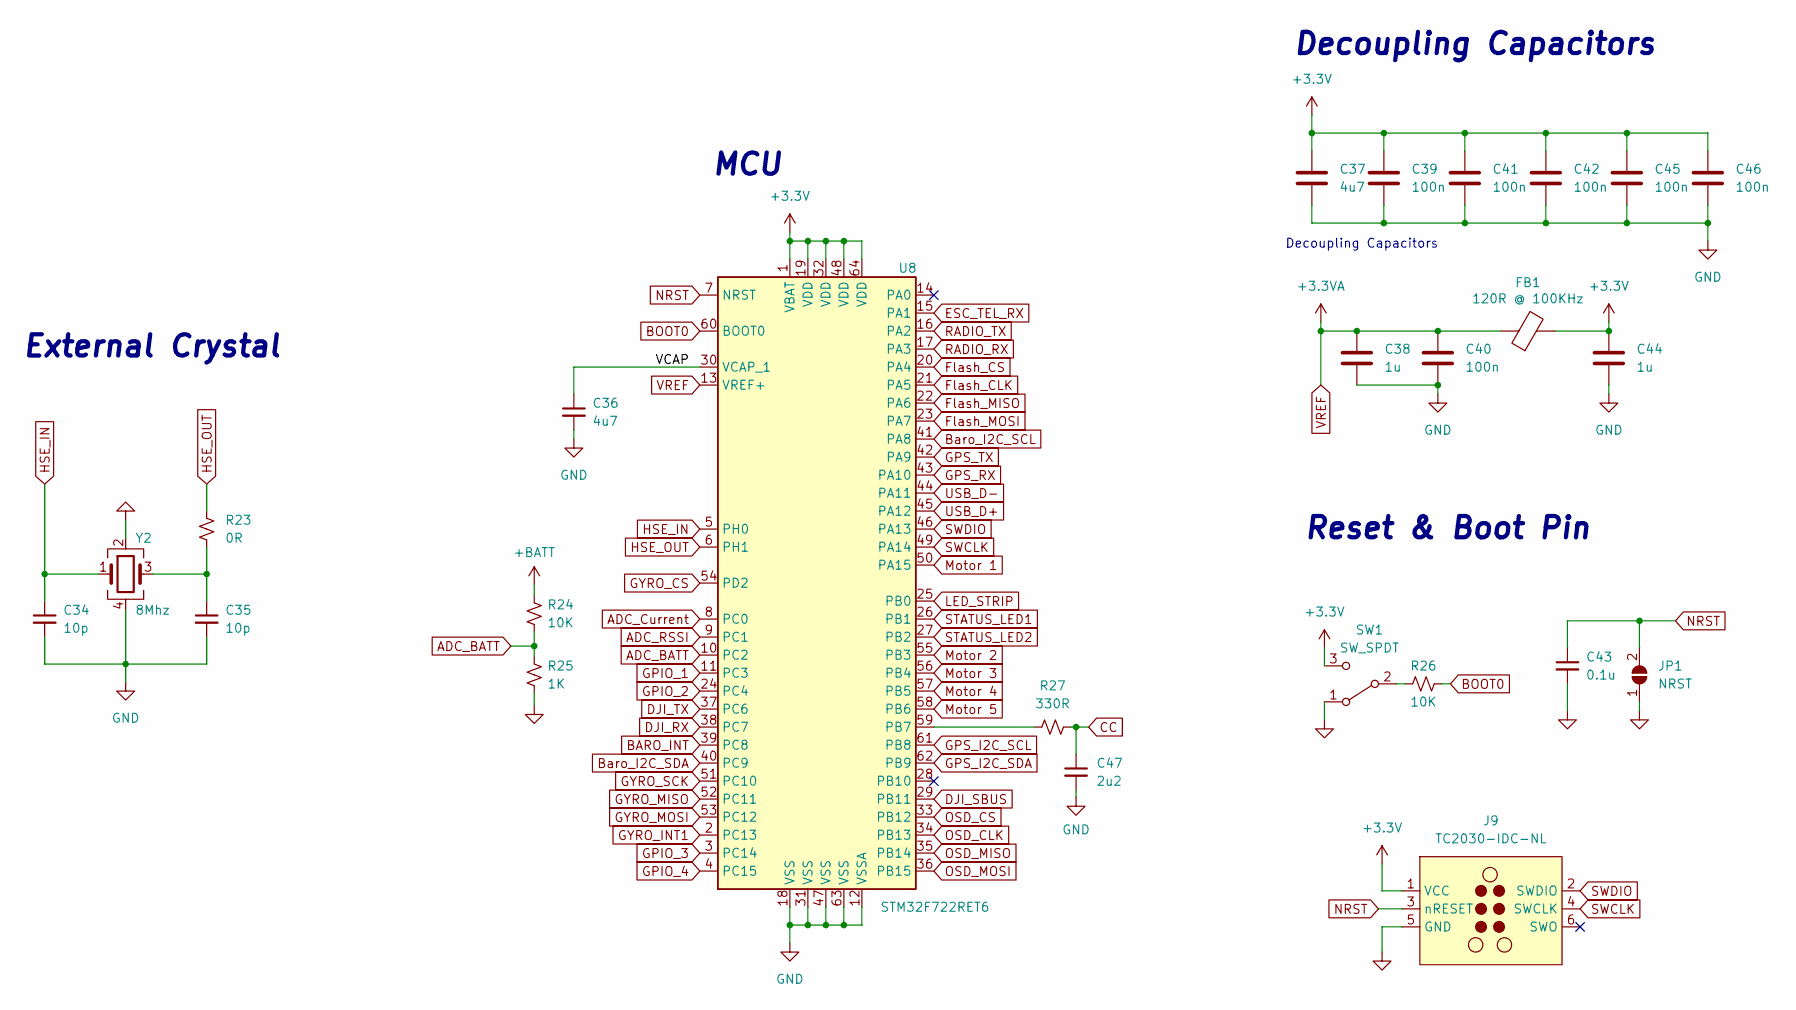
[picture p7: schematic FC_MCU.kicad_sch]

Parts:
C34, C35: 10p; C_0402_1005Metric
C36: 4u7; C_0603_1608Metric
C37: 4u7; C_0402_1005Metric
C38, C44: 1u; C_0402_1005Metric
C39, C40, C41, C42, C45, C46: 100n; C_0201_0603Metric
C43: 0.1u; C_0402_1005Metric
C47: 2u2; C_0603_1608Metric
FB1: 120R @ 100KHz; R_0603_1608Metric
J9: TC2030-IDC-NL; Tag-Connect_TC2030-IDC-NL_2x03_P1.27mm_Vertical
JP1: NRST; SolderJumper-2_P1.3mm_Open_TrianglePad1.0x1.5mm
R23: 0R; R_0402_1005Metric
R24: 10K; R_0201_0603Metric
R25: 1K; R_0201_0603Metric
R26: 10K; R_0402_1005Metric
R27: 330R; R_0603_1608Metric
SW1: SW_SPDT; SSSS810701
U8: STM32F722RET6; LQFP-64_10x10mm_P0.5mm
Y2: 8Mhz; Crystal_SMD_3225-4Pin_3.2x2.5mm

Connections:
+3V3: C37.1, C39.1, C41.1, C42.1, C44.1, C45.1, C46.1, FB1.2, J9.1 (VCC), SW1.3 (C), U8.1 (VBAT), U8.19 (VDD), U8.32 (VDD), U8.48 (VDD), U8.64 (VDD); also elsewhere on the board
+BATT: R24.1; also elsewhere on the board
/MCU/VCAP: C36.1, U8.30 (VCAP_1)
ADC_BATT: R24.2, R25.1, U8.10 (PC2)
ADC_Current: U8.8 (PC0); also elsewhere on the board
ADC_RSSI: U8.9 (PC1)
BARO_INT: U8.39 (PC8); also elsewhere on the board
BOOT0: R26.2, U8.60 (BOOT0)
Baro_I2C_SCL: U8.41 (PA8); also elsewhere on the board
Baro_I2C_SDA: U8.40 (PC9); also elsewhere on the board
CC: C47.1, R27.2; also elsewhere on the board
DJI_RX: U8.38 (PC7); also elsewhere on the board
DJI_SBUS: U8.29 (PB11); also elsewhere on the board
DJI_TX: U8.37 (PC6); also elsewhere on the board
ESC_TEL_RX: U8.15 (PA1); also elsewhere on the board
Flash_CLK: U8.21 (PA5); also elsewhere on the board
Flash_CS: U8.20 (PA4); also elsewhere on the board
Flash_MISO: U8.22 (PA6); also elsewhere on the board
Flash_MOSI: U8.23 (PA7); also elsewhere on the board
GND: C34.2, C35.2, C36.2, C37.2, C38.2, C39.2, C40.2, C41.2, C42.2, C43.2, C44.2, C45.2, C46.2, C47.2, J9.5 (GND), JP1.1 (A), R25.2, SW1.1 (A), U8.12 (VSSA), U8.18 (VSS), U8.31 (VSS), U8.47 (VSS), U8.63 (VSS), Y2.2, Y2.4; also elsewhere on the board
GPIO_1: U8.11 (PC3); also elsewhere on the board
GPIO_2: U8.24 (PC4); also elsewhere on the board
GPIO_3: U8.3 (PC14); also elsewhere on the board
GPIO_4: U8.4 (PC15); also elsewhere on the board
GPS_I2C_SCL: U8.61 (PB8); also elsewhere on the board
GPS_I2C_SDA: U8.62 (PB9); also elsewhere on the board
GPS_RX: U8.43 (PA10); also elsewhere on the board
GPS_TX: U8.42 (PA9); also elsewhere on the board
GYRO_CS: U8.54 (PD2); also elsewhere on the board
GYRO_INT1: U8.2 (PC13); also elsewhere on the board
GYRO_MISO: U8.52 (PC11); also elsewhere on the board
GYRO_MOSI: U8.53 (PC12); also elsewhere on the board
GYRO_SCK: U8.51 (PC10); also elsewhere on the board
HSE_IN: C34.1, U8.5 (PH0), Y2.1
HSE_OUT: R23.1, U8.6 (PH1)
LED_STRIP: U8.25 (PB0); also elsewhere on the board
Motor 1: U8.50 (PA15); also elsewhere on the board
Motor 2: U8.55 (PB3); also elsewhere on the board
Motor 3: U8.56 (PB4); also elsewhere on the board
Motor 4: U8.57 (PB5); also elsewhere on the board
Motor 5: U8.58 (PB6); also elsewhere on the board
NRST: C43.1, J9.3 (nRESET), JP1.2 (B), U8.7 (NRST)
unnamed: C35.1, R23.2, Y2.3
unnamed: R26.1, SW1.2 (B)
unnamed: R27.1, U8.59 (PB7)
OSD_CLK: U8.34 (PB13); also elsewhere on the board
OSD_CS: U8.33 (PB12); also elsewhere on the board
OSD_MISO: U8.35 (PB14); also elsewhere on the board
OSD_MOSI: U8.36 (PB15); also elsewhere on the board
RADIO_RX: U8.17 (PA3); also elsewhere on the board
RADIO_TX: U8.16 (PA2); also elsewhere on the board
STATUS_LED1: U8.26 (PB1); also elsewhere on the board
STATUS_LED2: U8.27 (PB2); also elsewhere on the board
SWCLK: J9.4 (SWCLK), U8.49 (PA14)
SWDIO: J9.2 (SWDIO), U8.46 (PA13)
USB_D+: U8.45 (PA12); also elsewhere on the board
USB_D-: U8.44 (PA11); also elsewhere on the board
VREF: C38.1, C40.1, FB1.1, U8.13 (VREF+)

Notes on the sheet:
External Crystal
MCU
Decoupling Capacitors
Reset & Boot Pin

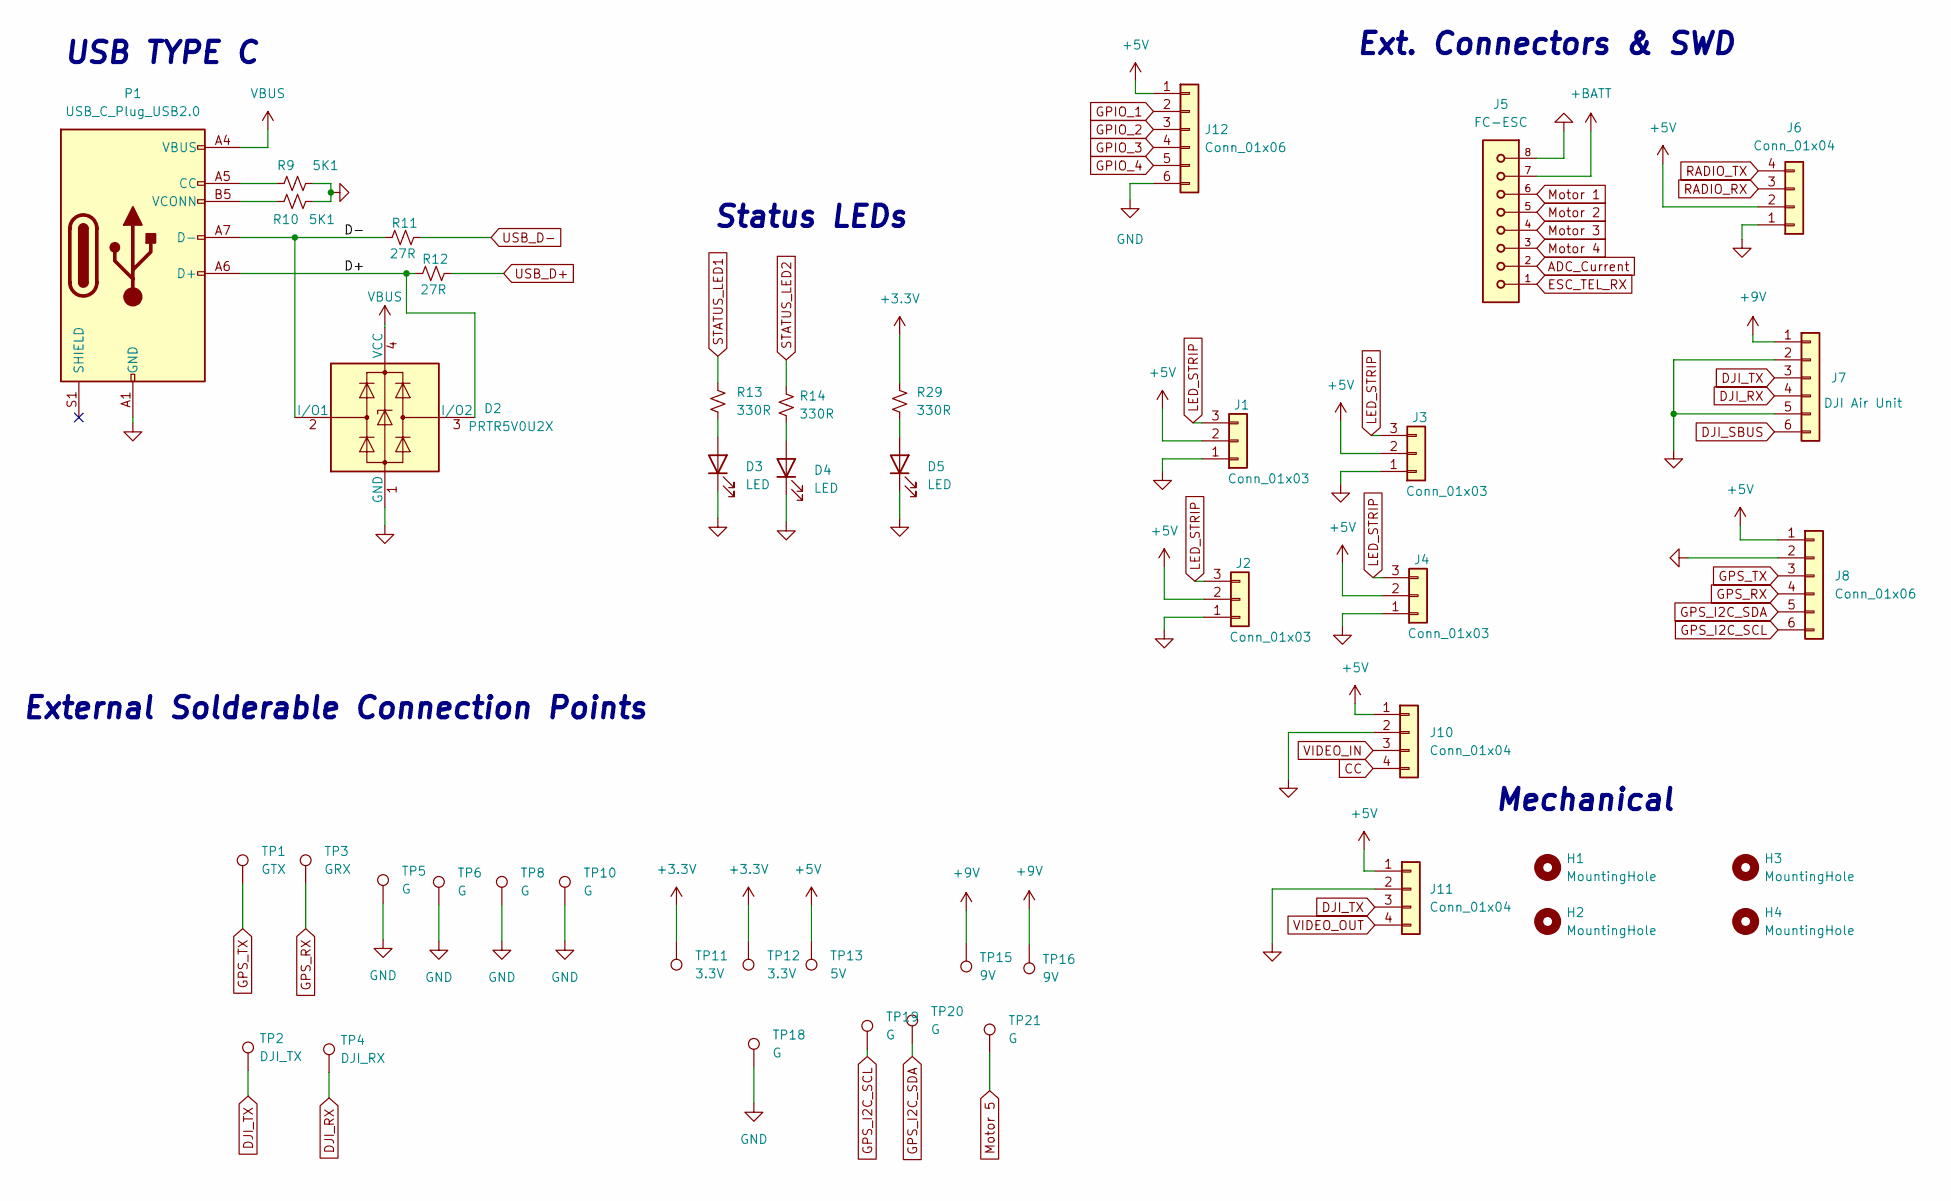
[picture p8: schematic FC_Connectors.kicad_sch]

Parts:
D2: PRTR5V0U2X; SOT-143
D3, D4, D5: LED; LED_0402_1005Metric
H1, H2, H3, H4: MountingHole; MountingHole_2.2mm_M2_Pad_Via
J1, J2, J3, J4: Conn_01x03; JST_SH_SM03B-SRSS-TB_1x03-1MP_P1.00mm_Horizontal
J5: FC-ESC; JST_SH_SM08B-SRSS-TB_1x08-1MP_P1.00mm_Horizontal
J6, J10, J11: Conn_01x04; JST_SH_SM04B-SRSS-TB_1x04-1MP_P1.00mm_Horizontal
J7: DJI Air Unit; JST_SH_SM06B-SRSS-TB_1x06-1MP_P1.00mm_Horizontal
J8, J12: Conn_01x06; JST_SH_SM06B-SRSS-TB_1x06-1MP_P1.00mm_Horizontal
P1: USB_C_Plug_USB2.0; USB4110GFA
R9, R10: 5K1; R_0201_0603Metric
R11, R12: 27R; R_0201_0603Metric
R13, R14, R29: 330R; R_0402_1005Metric
TP1: GTX; Solderable Point
TP2: DJI_TX; Solderable Point
TP3: GRX; Solderable Point
TP4: DJI_RX; Solderable Point
TP5, TP6, TP8, TP10, TP18, TP19, TP20, TP21: G; Solderable Point
TP11, TP12: 3.3V; Solderable Point
TP13: 5V; Solderable Point
TP15, TP16: 9V; Solderable Point

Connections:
+3V3: R29.1, TP11.1, TP12.1; also elsewhere on the board
+5V: J1.2, J2.2, J3.2, J4.2, J6.2, J8.1, J10.1, J11.1, J12.1, TP13.1; also elsewhere on the board
+9V: J7.1, TP15.1, TP16.1; also elsewhere on the board
+BATT: J5.7; also elsewhere on the board
/Connectors/D+: D2.3 (I/O2), P1.A6 (D+), R12.1
/Connectors/D-: D2.2 (I/O1), P1.A7 (D-), R11.1
ADC_Current: J5.2; also elsewhere on the board
CC: J10.4; also elsewhere on the board
DJI_RX: J7.4, TP4.1; also elsewhere on the board
DJI_SBUS: J7.6; also elsewhere on the board
DJI_TX: J7.3, J11.3, TP2.1; also elsewhere on the board
ESC_TEL_RX: J5.1; also elsewhere on the board
GND: D2.1 (GND), D3.1 (K), D4.1 (K), D5.1 (K), J1.1, J2.1, J3.1, J4.1, J5.8, J6.1, J7.2, J7.5, J8.2, J10.2, J11.2, J12.6, P1.A1 (GND), P1.A12 (GND), P1.B1 (GND), P1.B12 (GND), R9.1, R10.2, TP5.1, TP6.1, TP8.1, TP10.1, TP18.1; also elsewhere on the board
GPIO_1: J12.2; also elsewhere on the board
GPIO_2: J12.3; also elsewhere on the board
GPIO_3: J12.4; also elsewhere on the board
GPIO_4: J12.5; also elsewhere on the board
GPS_I2C_SCL: J8.6, TP19.1; also elsewhere on the board
GPS_I2C_SDA: J8.5, TP20.1; also elsewhere on the board
GPS_RX: J8.4, TP3.1; also elsewhere on the board
GPS_TX: J8.3, TP1.1; also elsewhere on the board
LED_STRIP: J1.3, J2.3, J3.3, J4.3; also elsewhere on the board
Motor 1: J5.6; also elsewhere on the board
Motor 2: J5.5; also elsewhere on the board
Motor 3: J5.4; also elsewhere on the board
Motor 4: J5.3; also elsewhere on the board
Motor 5: TP21.1; also elsewhere on the board
unnamed: D3.2 (A), R13.2
unnamed: D4.2 (A), R14.2
unnamed: D5.2 (A), R29.2
unnamed: P1.A5 (CC), R9.2
unnamed: P1.B5 (VCONN), R10.1
RADIO_RX: J6.3; also elsewhere on the board
RADIO_TX: J6.4; also elsewhere on the board
STATUS_LED1: R13.1; also elsewhere on the board
STATUS_LED2: R14.1; also elsewhere on the board
USB_D+: R12.2; also elsewhere on the board
USB_D-: R11.2; also elsewhere on the board
VBUS: D2.4 (VCC), P1.A4 (VBUS), P1.A9 (VBUS), P1.B4 (VBUS), P1.B9 (VBUS); also elsewhere on the board
VIDEO_IN: J10.3; also elsewhere on the board
VIDEO_OUT: J11.4; also elsewhere on the board

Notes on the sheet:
USB TYPE C
Status LEDs
Ext. Connectors & SWD
External Solderable Connection Points
Mechanical

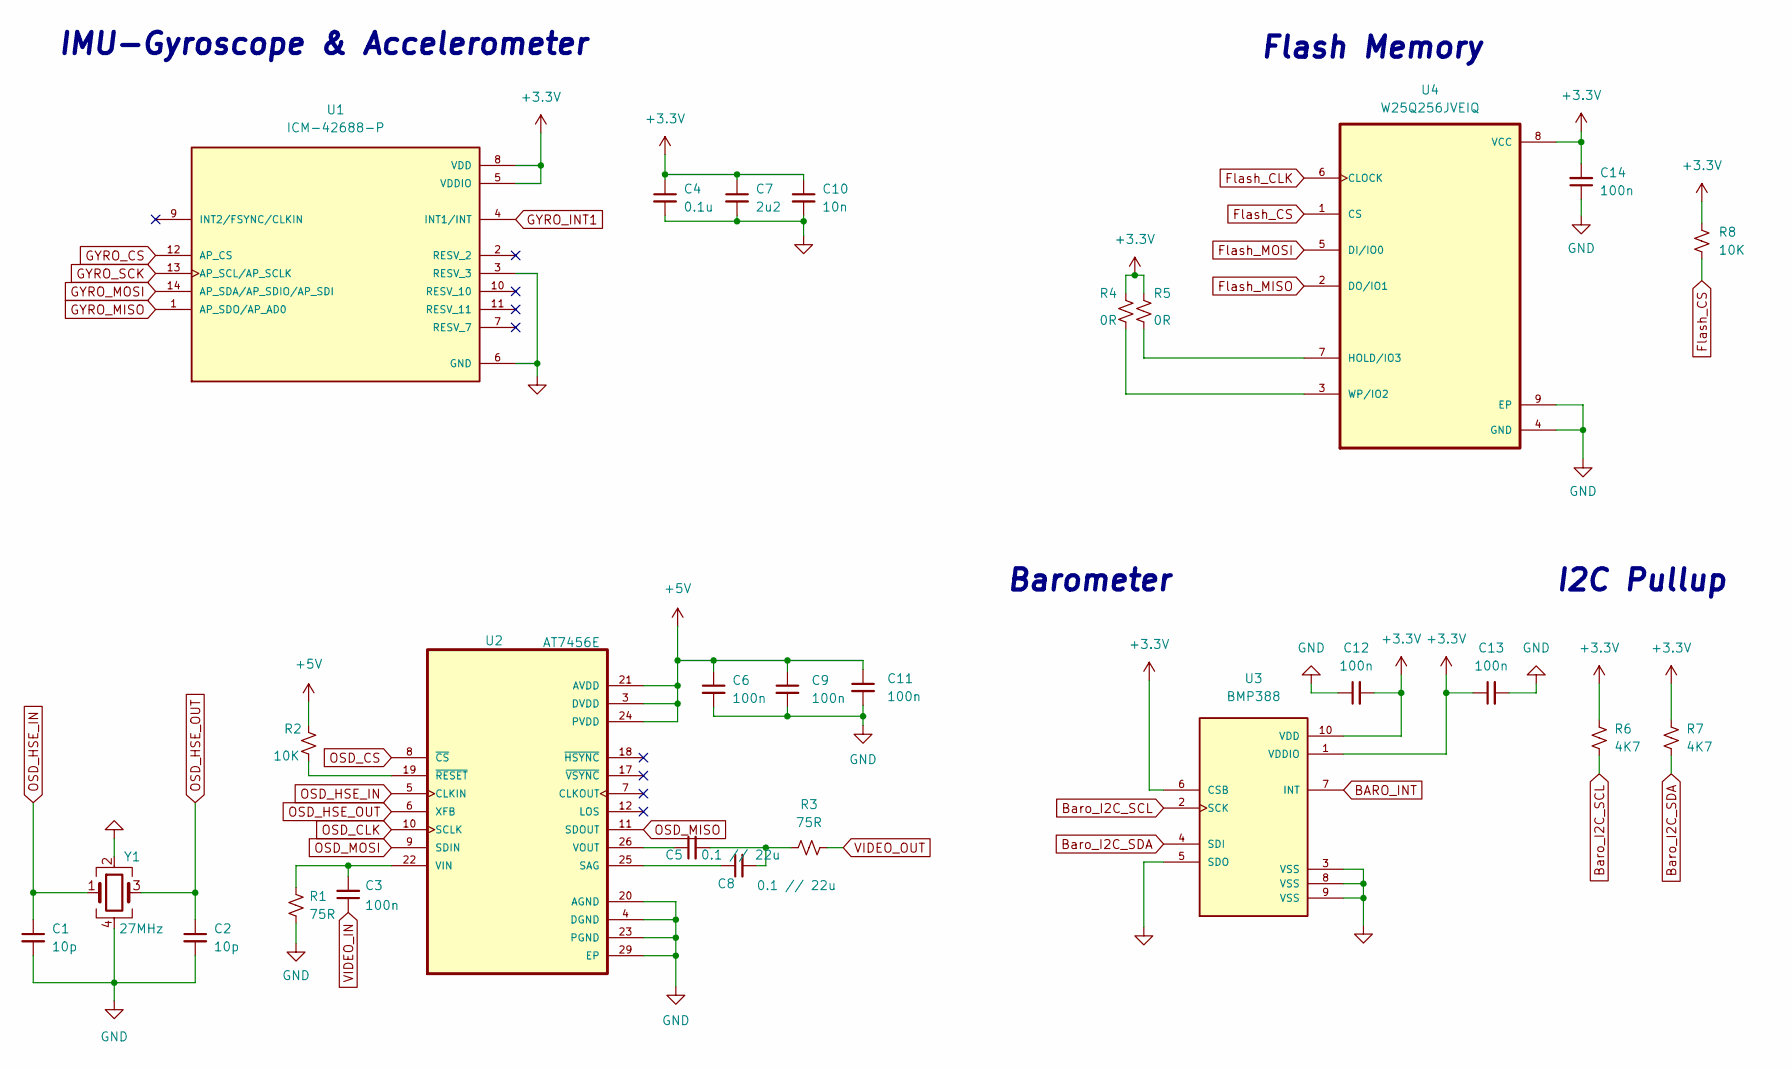
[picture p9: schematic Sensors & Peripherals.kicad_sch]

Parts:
C1, C2: 10p; C_0201_0603Metric
C3, C6, C9, C11, C12, C13: 100n; C_0201_0603Metric
C4: 0.1u; C_0402_1005Metric
C5, C8: 0.1 // 22u; C_0201_0603Metric
C7: 2u2; C_0603_1608Metric
C10: 10n; C_0201_0603Metric
C14: 100n; C_0402_1005Metric
R1, R3: 75R; R_0201_0603Metric
R2, R8: 10K; R_0201_0603Metric
R4, R5: 0R; R_0201_0603Metric
R6, R7: 4K7; R_0201_0603Metric
U1: ICM-42688-P; ICP-42688-P; PARTREV 1.2
U2: AT7456E; SOP65P637X110-28N
U3: BMP388; PARTREV 1.1
U4: W25Q256JVEIQ; SON127P600X800X80-9N
Y1: 27MHz; Crystal_SMD_3225-4Pin_3.2x2.5mm

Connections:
+3V3: C4.1, C7.1, C10.1, C12.2, C13.1, C14.2, R4.1, R5.1, R6.1, R7.1, R8.1, U1.5 (VDDIO), U1.8 (VDD), U3.1 (VDDIO), U3.6 (CSB), U3.10 (VDD), U4.8 (VCC); also elsewhere on the board
+5V: C6.1, C9.1, C11.1, R2.2, U2.3 (DVDD), U2.21 (AVDD), U2.24 (PVDD); also elsewhere on the board
BARO_INT: U3.7 (INT); also elsewhere on the board
Baro_I2C_SCL: R6.2, U3.2 (SCK); also elsewhere on the board
Baro_I2C_SDA: R7.2, U3.4 (SDI); also elsewhere on the board
Flash_CLK: U4.6 (CLOCK); also elsewhere on the board
Flash_CS: R8.2, U4.1 (CS); also elsewhere on the board
Flash_MISO: U4.2 (DO/IO1); also elsewhere on the board
Flash_MOSI: U4.5 (DI/IO0); also elsewhere on the board
GND: C1.2, C2.2, C4.2, C6.2, C7.2, C9.2, C10.2, C11.2, C12.1, C13.2, C14.1, R1.2, U1.3 (RESV_3), U1.6 (GND), U2.4 (DGND), U2.20 (AGND), U2.23 (PGND), U2.29 (EP), U3.3 (VSS), U3.5 (SDO), U3.8 (VSS), U3.9 (VSS), U4.4 (GND), U4.9 (EP), Y1.2, Y1.4; also elsewhere on the board
GYRO_CS: U1.12 (AP_CS); also elsewhere on the board
GYRO_INT1: U1.4 (INT1/INT); also elsewhere on the board
GYRO_MISO: U1.1 (AP_SDO/AP_AD0); also elsewhere on the board
GYRO_MOSI: U1.14 (AP_SDA/AP_SDIO/AP_SDI); also elsewhere on the board
GYRO_SCK: U1.13 (AP_SCL/AP_SCLK); also elsewhere on the board
unnamed: C3.2, R1.1, U2.22 (VIN)
unnamed: C5.1, U2.26 (VOUT)
unnamed: C5.2, C8.2, R3.1
unnamed: C8.1, U2.25 (SAG)
unnamed: R2.1, U2.19 (~RESET)
unnamed: R4.2, U4.3 (WP/IO2)
unnamed: R5.2, U4.7 (HOLD/IO3)
OSD_CLK: U2.10 (SCLK); also elsewhere on the board
OSD_CS: U2.8 (~CS); also elsewhere on the board
OSD_HSE_IN: C1.1, U2.5 (CLKIN), Y1.1
OSD_HSE_OUT: C2.1, U2.6 (XFB), Y1.3
OSD_MISO: U2.11 (SDOUT); also elsewhere on the board
OSD_MOSI: U2.9 (SDIN); also elsewhere on the board
VIDEO_IN: C3.1; also elsewhere on the board
VIDEO_OUT: R3.2; also elsewhere on the board

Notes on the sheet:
I2C Pullup
Flash Memory
IMU-Gyroscope & Accelerometer
Barometer

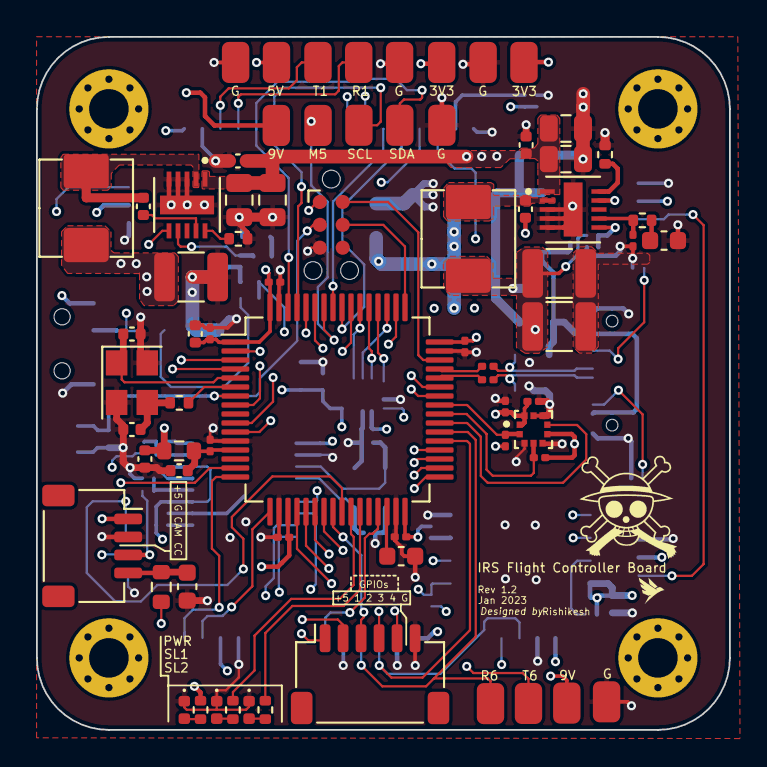
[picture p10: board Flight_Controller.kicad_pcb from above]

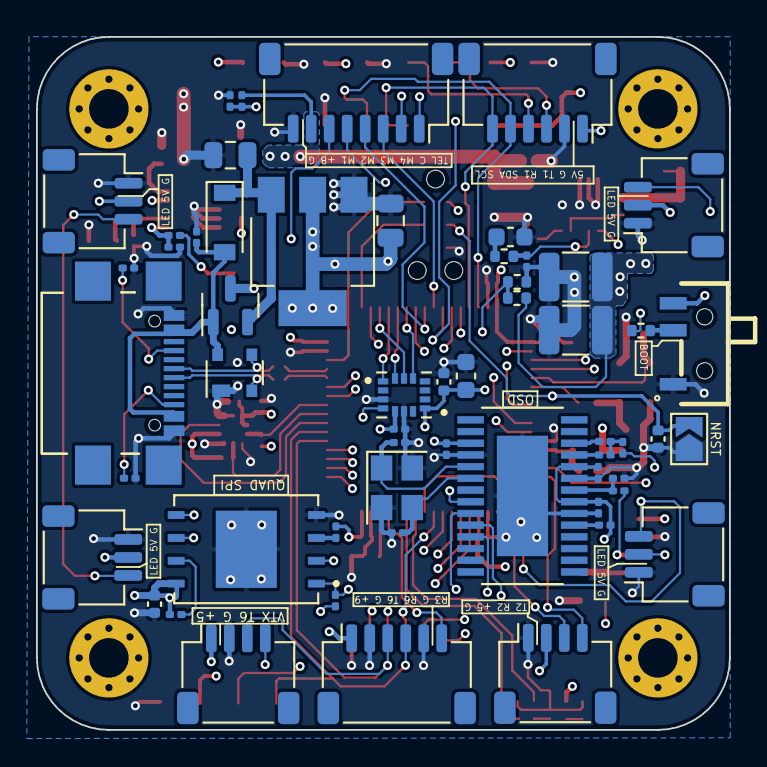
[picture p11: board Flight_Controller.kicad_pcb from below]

Board: 8 copper layers, 38.5 x 38.5 mm, 131 parts (56 on the bottom side), 91 nets.

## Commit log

2023-03-04 Create bom
2023-03-04 Create gerber
